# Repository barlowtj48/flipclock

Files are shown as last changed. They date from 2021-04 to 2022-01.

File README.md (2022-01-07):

# Smart Flip Clock
3D printed smart clock that puts a new twist on old technology.

Smart Flip Clock

# Making The Smart Flip Clock
The first thing that must be done for this project is to obtain all the materials that will be used. The list of things needed in this project are:
- Raspberry Pi Zero W (or any raspberry pi)
- Adequate Power Supply for Pi
- Stepper Motors (linked below)
- 3D printer and filament
- Wire
- Ability to Solder
- Glue
- Mechanical key switch from a keyboard

This design uses 4 stepper motors that can be powered using a Raspberry Pi. An external power supply is better, however they will work fine without one. The motors that I used in this project are the 28byj-48 steppers. They can be powered using 5v.

They can be found on Amazon at this link. https://www.amazon.com/gp/product/B015RQ97W8/ref=ppx_yo_dt_b_search_asin_title?ie=UTF8&psc=1

The entire construction of this clock is 3D printed, including the numbers and symbols on the flaps. Drawing on the flaps, or using stickers would be much easier however.

After printing the parts that are found on this GitHub, they can be assembled to fit together. The only thing that needs adjustment is the very small piece of plastic that is used to hold each flap in position. By design, this piece is meant to be bent after the fact to an amount that holds them sufficiently. Here's the correct number of parts that you'll need for the full assembly. If they are not listed, you only need 1 of them. 

- 56 Flaps
- 4 Drive Plates
- 4 Top Rings (to hold each of the 14 flaps onto their central shaft)
- 4 Flap Gear shafts
- 4 Drive Gears
- 4 Idle Gears
- 4 Idle Gear Holders (look like washers)
- 8 Bolts (printed)
- 4 Frame braces (optional if you're using the flap restrictor)

For the larger parts, I've included 2 options for those who are trying to print this with a smaller print bed. Option 1 is to come up with something on your own, and use the STEP files that are in the STEP files folder. Option 2 is to use the parts labeled `clock_part_split0.stl`. These are cut up to fit onto beds that are 150mm, to make sure that everyone can print them. 

In the code (and before putting labels on), make sure to test the code after plugging in the motors. If they do not rotate smoothly, you have likely ordered the pins incorrectly. Add a `time.sleep(1)` command where the clock increments each step of the motor. This will indicate what stage in the step that the motor is in. The LEDs on the controller board should light up to reflect its current stage. They should follow this order. 1 for on, 0 for off. 

0:   `1 0 0 0`\
1:   `1 1 0 0`\
2:   `0 1 0 0`\
3:   `0 1 1 0`\
4:   `0 0 1 0`\
5:   `0 0 1 1`\
6:   `0 0 0 1`\
7:   `1 0 0 1`

If this is not true, ensure that the correct pins are in order in the code. 

After this holds true for all 4 steppers, then you are good to attack the motors to the clock frame with the plastic bolts and glue.

A button is also included, I used an old mechanical key switch that was laying around. This is used to operate the clock.
It is connected as a closed loop to the raspberry pi. The switch is attached to GPIO pin 24, and to ground. The orientation should not matter. It is used as a trigger in the code to display the weather, and pause/stop the clock when held for longer durations. 

Make sure that the following packages are installed on the system, so that the code is able to locate itself and give accurate weather information. This is done with the following commands. 
`sudo pip3 install geocoder`
For the Pi Zero, the following command must be run to obtain the GPIO package.
`sudo apt-get update
sudo apt-get install rpi.gpio`

Before the code will run, you must first obtain an API key from https://openweathermap.org/api (free). This is needed to fetch the weather for your area. Take the key that is generated from your account, and put it in the place of `api_key = "YOUR_API_KEY_HERE"` in the code (line 122). This will give the python code access to the weather data. 

Upload the code to the Pi, and run the command `sudo nohup flipclock.py`. This will get the code to run in the background on the pi. 

There are 4 "modes" of the clock. Right as the script starts, it's in its default mode of showing the time. When the button is pressed, it will show the weather for an amount of time you can set for yourself, default is 10 seconds. To pause the clock, hold the button for more than 2 seconds but less than 10. To unpause, just press the button again. To set the flaps back to their 'resting' state, 0000, hold the button for 10 seconds. This will also end the python script.

## Assembly
If you've printed the number of pieces directed above, then assembly should be a relatively-simple puzzle to assemble. To assist, here are photos of the rear of my clock that should help to clear up any confusion if you have any.

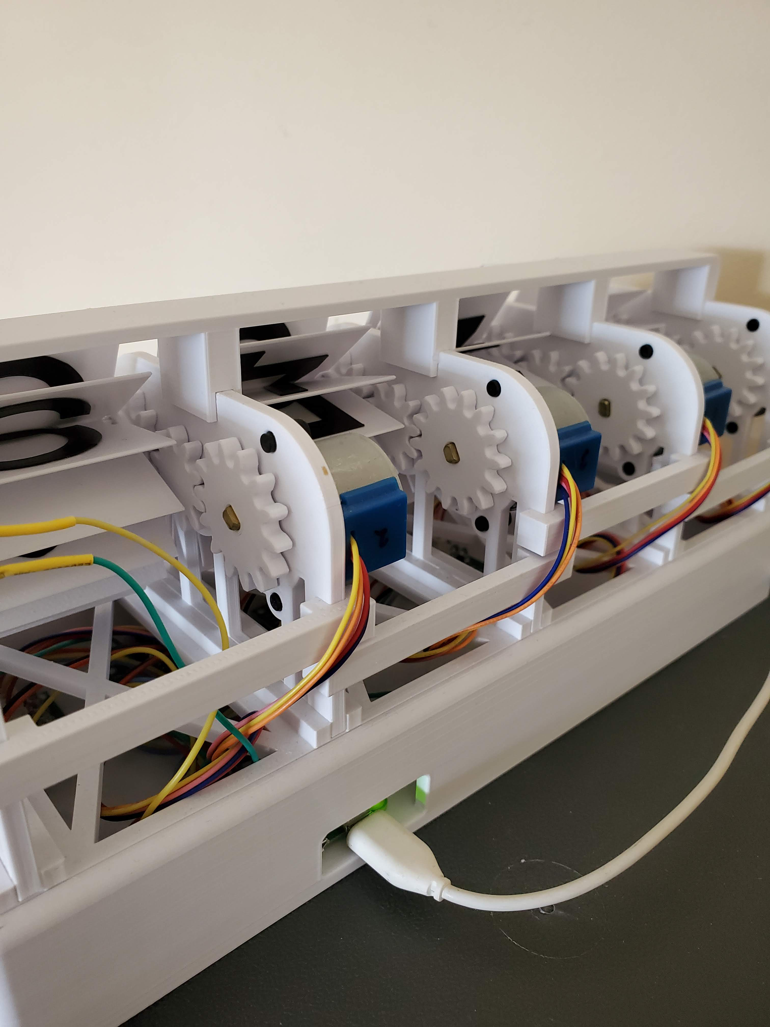
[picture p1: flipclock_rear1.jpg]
Flipclock Rear Photo 1


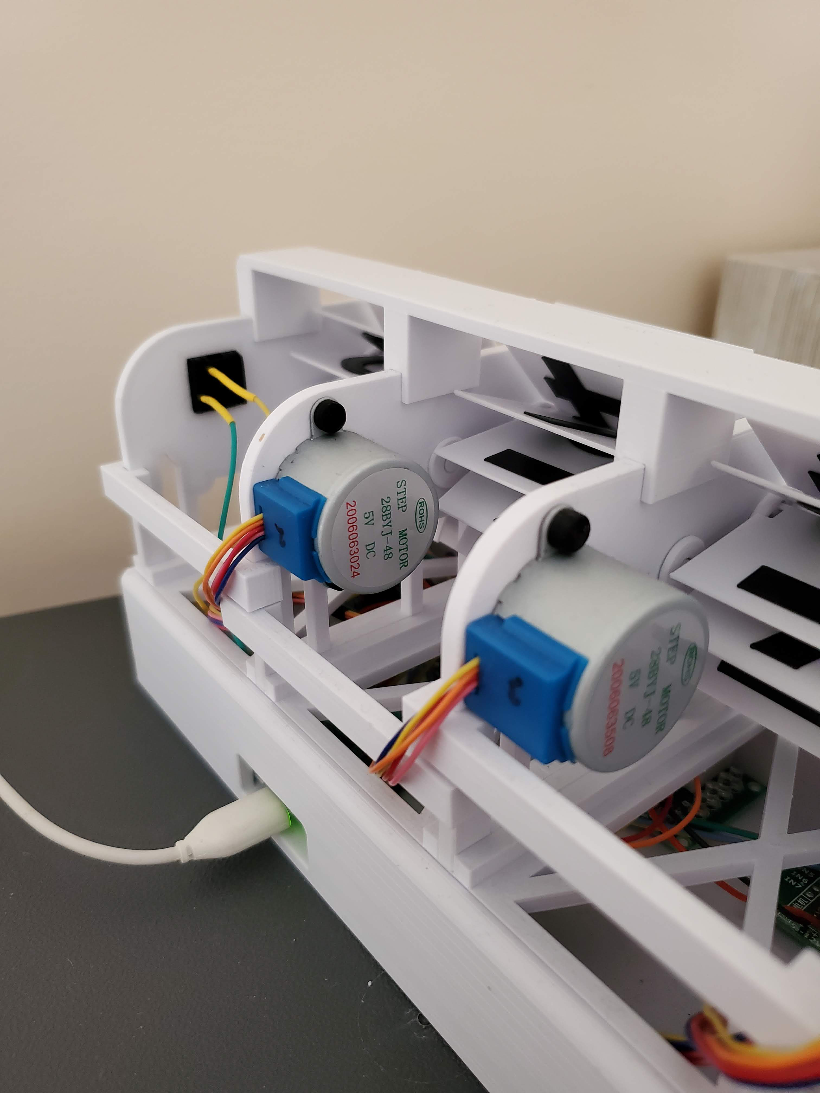
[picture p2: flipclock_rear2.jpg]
Flipclock Rear Photo 2


To read more about my time designing this and printing it, visit [my website](https://thomasjbarlow.com/flip_clock).
If you have any questions about this, feel free to email me! You can find my email easily from the above link.

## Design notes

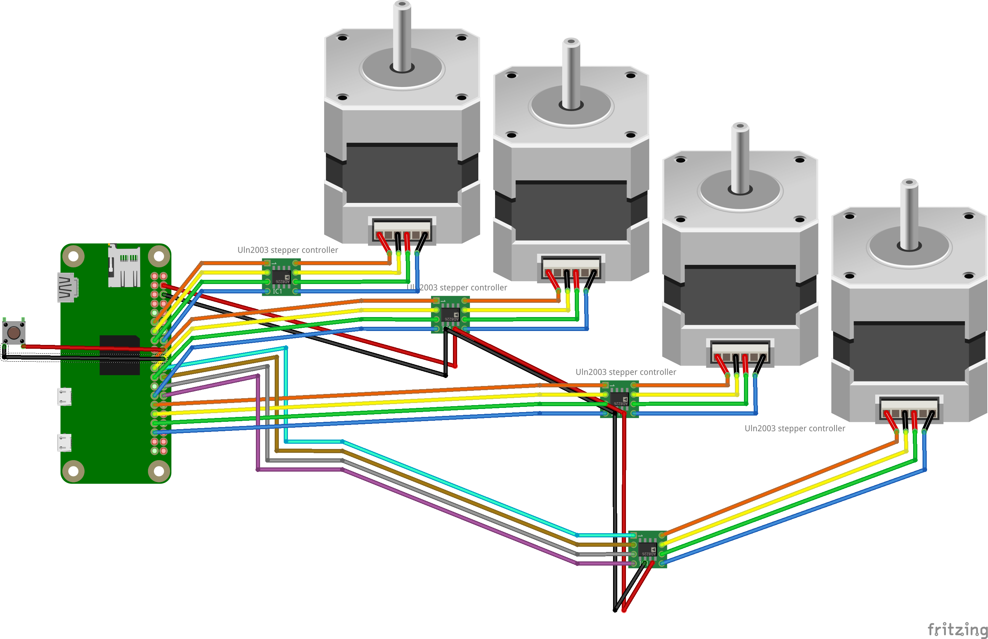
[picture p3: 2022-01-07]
flipclock_schematic.png

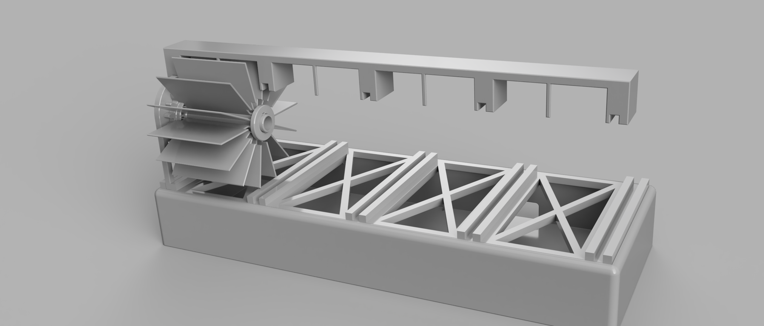
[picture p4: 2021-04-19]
flip_clock_stls/Render/FlipClock_Frame_2021-Jan-27_08-05-05PM-000_CustomizedView24092891461.png

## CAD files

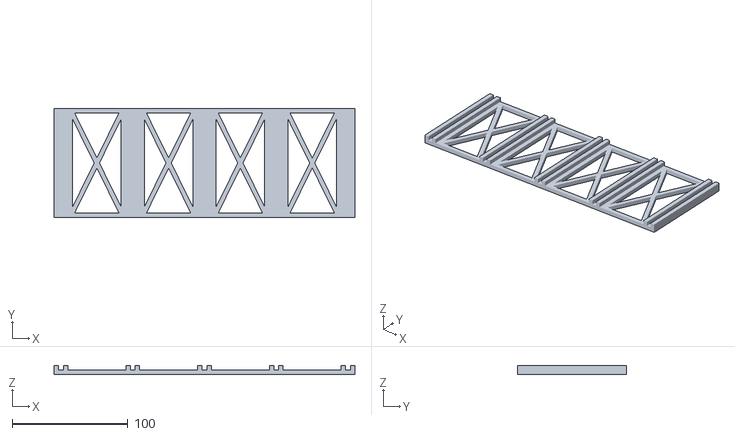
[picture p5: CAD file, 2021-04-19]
flip_clock_stls/FullFrameBrace.stl
260.0 x 94.0 x 8.00

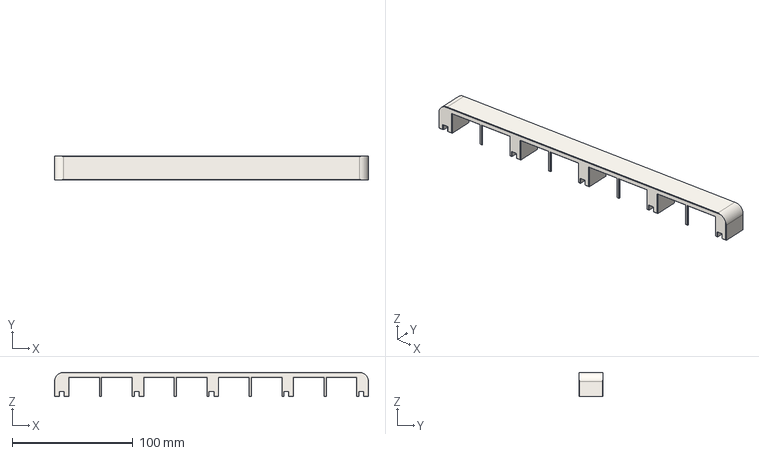
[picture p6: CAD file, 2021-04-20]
flip_clock_step/FlipClock_Flip_Restrictor.step
260.0 x 20.0 x 20.0 mm

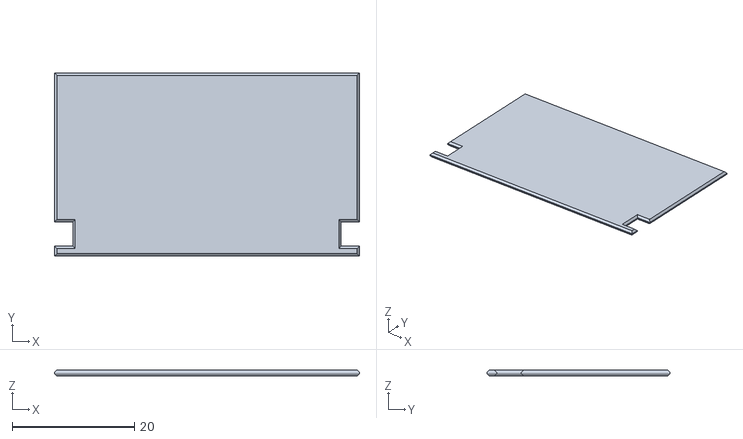
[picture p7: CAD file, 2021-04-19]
flip_clock_stls/Flap.stl
50.0 x 30.0 x 1.00

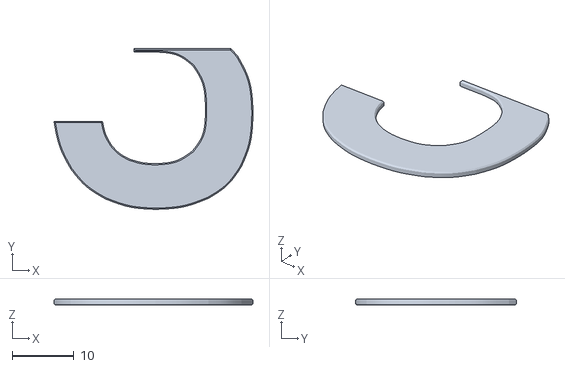
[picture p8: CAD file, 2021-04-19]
flip_clock_stls/Numbers/three2.stl
32.3 x 26.1 x 1.00

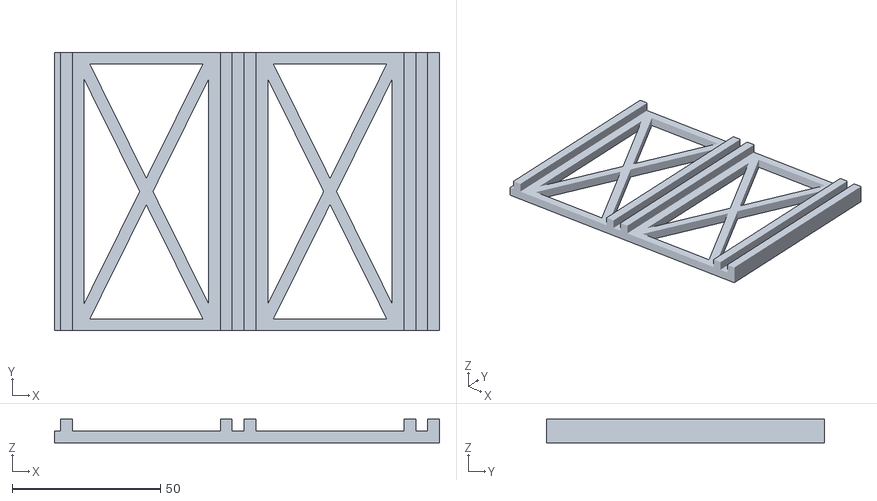
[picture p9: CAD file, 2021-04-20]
flip_clock_stls/split_parts/FrameBrace_split0.stl
130.0 x 94.0 x 8.00

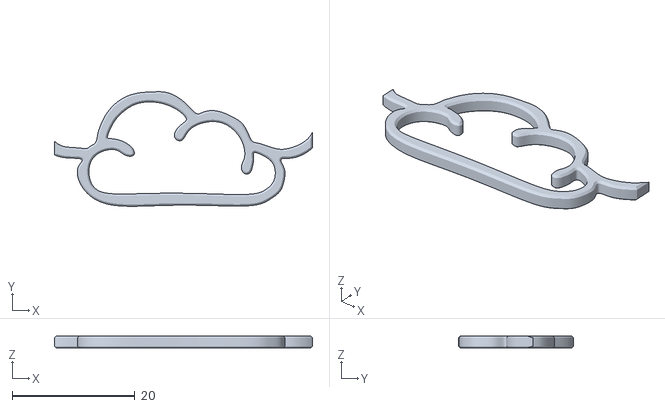
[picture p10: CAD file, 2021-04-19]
flip_clock_stls/Symbols/13_4.stl
42.0 x 18.7 x 2.00

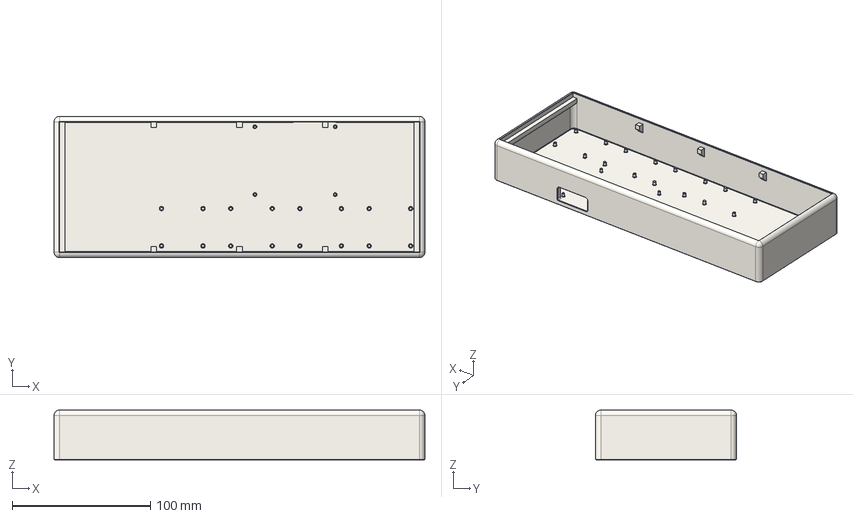
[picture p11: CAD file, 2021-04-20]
flip_clock_step/FlipClock_Base.step
268.0 x 102.0 x 36.0 mm

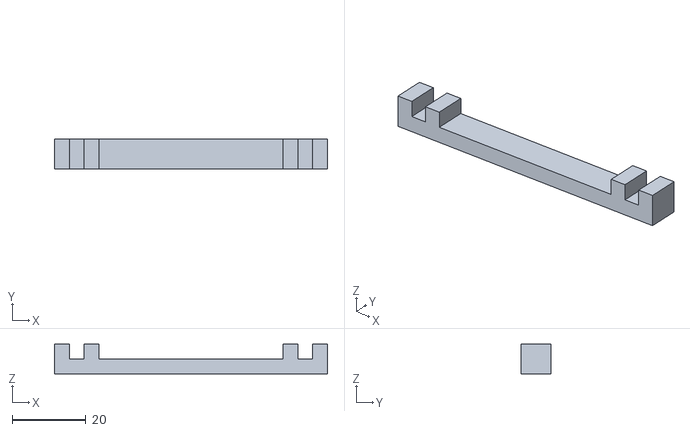
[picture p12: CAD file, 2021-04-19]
flip_clock_stls/FrameBrace.stl
74.0 x 8.00 x 8.00

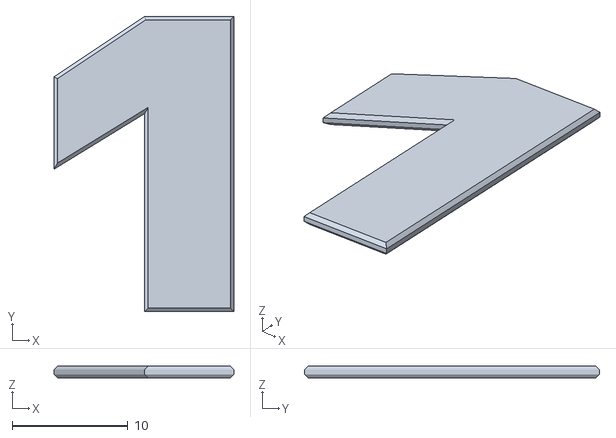
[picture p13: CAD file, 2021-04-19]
flip_clock_stls/Numbers/one1.stl
15.5 x 25.5 x 1.00

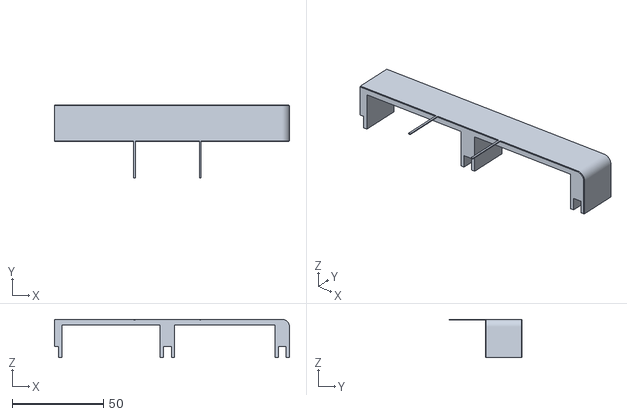
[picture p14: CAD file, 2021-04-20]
flip_clock_stls/split_parts/FlipRestrictor_split0.stl
129.0 x 40.0 x 21.0

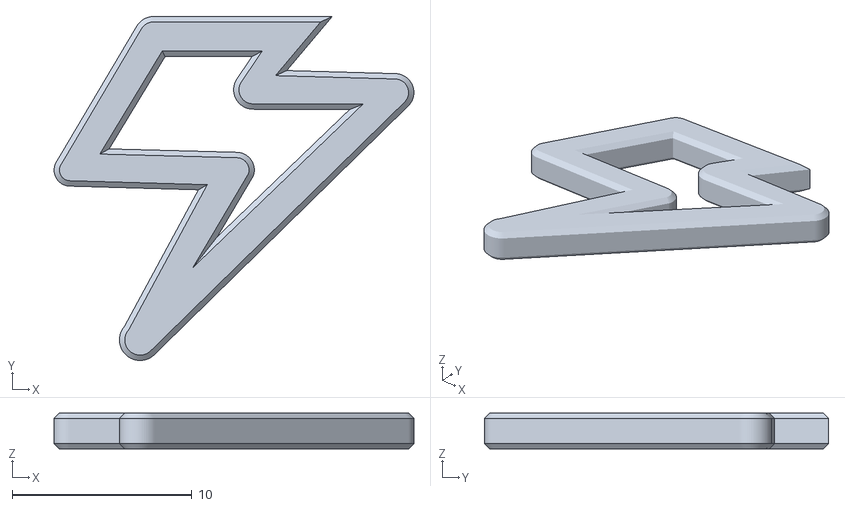
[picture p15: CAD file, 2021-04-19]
flip_clock_stls/Symbols/11_5.stl
20.0 x 19.1 x 2.00

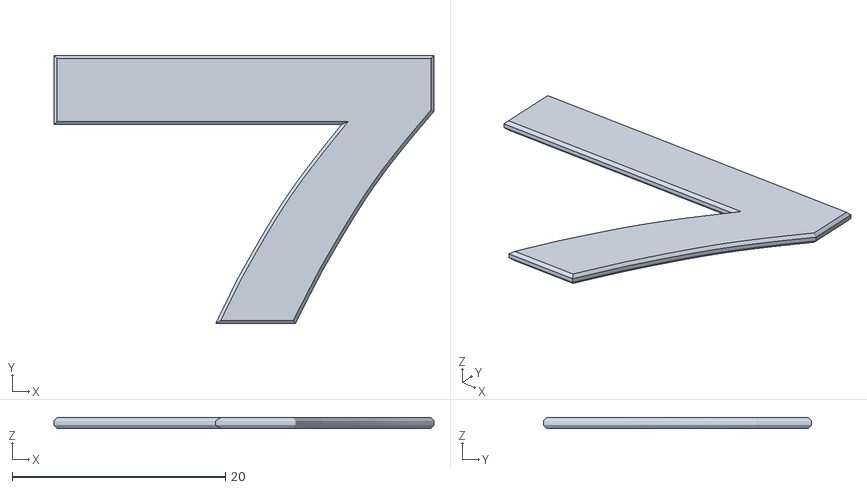
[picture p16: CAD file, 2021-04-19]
flip_clock_stls/Numbers/seven1.stl
35.6 x 25.1 x 1.00

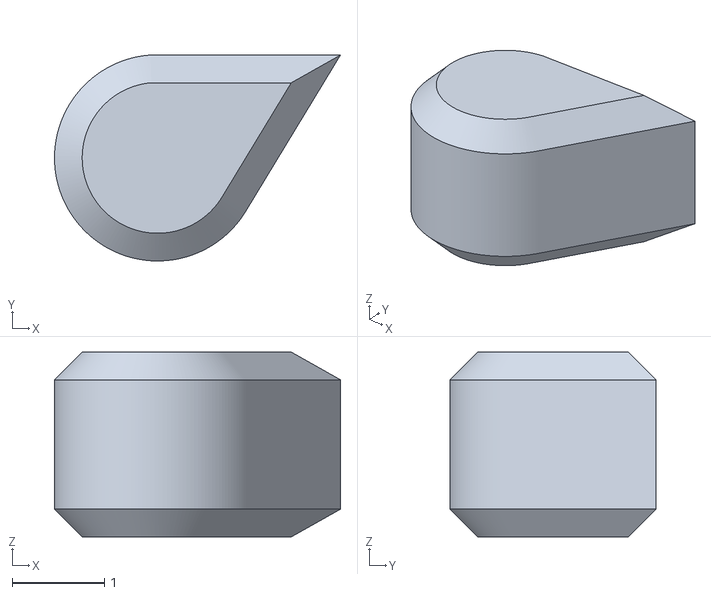
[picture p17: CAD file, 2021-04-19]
flip_clock_stls/Symbols/9_5.stl
3.09 x 2.23 x 2.00

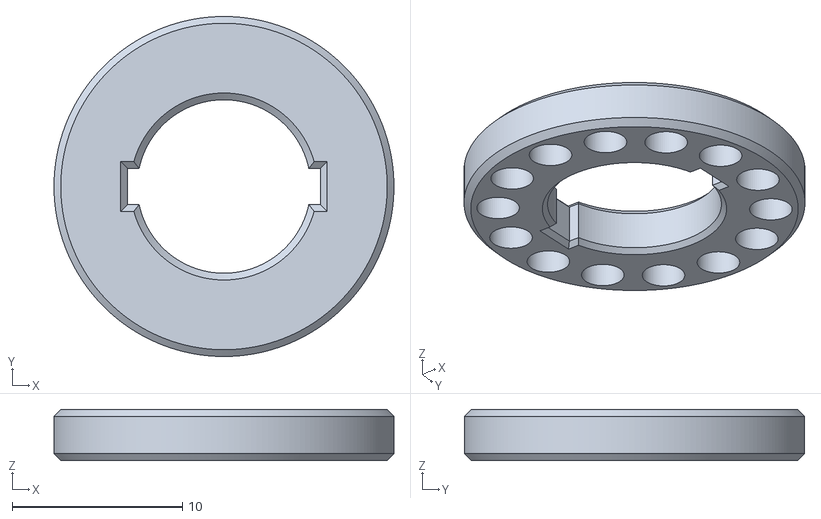
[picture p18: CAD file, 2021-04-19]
flip_clock_stls/TopRing.stl
20.0 x 20.0 x 3.00

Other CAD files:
flip_clock_step/FlipClock_FrameBase.step
flip_clock_stls/split_parts/FlipRestrictor_split1.stl
flip_clock_stls/IdleGearHolder.stl
flip_clock_stls/Numbers/five2.stl
flip_clock_stls/Bolt.stl
flip_clock_stls/Button.stl
flip_clock_stls/ButtonPlate.stl
flip_clock_stls/DriveGear.stl
flip_clock_stls/DrivePlate.stl
flip_clock_stls/FlapGear.stl
flip_clock_stls/FlipRestrictor.stl
flip_clock_stls/FrameBody.stl
flip_clock_stls/IdleGear.stl
flip_clock_stls/Numbers/eight1.stl
flip_clock_stls/Numbers/eight2.stl
flip_clock_stls/Numbers/five1.stl
flip_clock_stls/Numbers/four1.stl
flip_clock_stls/Numbers/four2.stl
flip_clock_stls/Numbers/four3.stl
flip_clock_stls/Numbers/nine1.stl
flip_clock_stls/Numbers/nine2.stl
flip_clock_stls/Numbers/nine3.stl
flip_clock_stls/Numbers/one2.stl
flip_clock_stls/Numbers/seven2.stl
flip_clock_stls/Numbers/six1.stl
flip_clock_stls/Numbers/six2.stl
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

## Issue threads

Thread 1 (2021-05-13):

How to synchronize flaps position with time and weather

SemperVis, 2021-05-13:
Hi! First of all, great project! I think it looks really cool and it's a fun thing to print or to gift.

That said, I'm having a bit of an hard time trying to synchronize the position of the flaps with the time and the weather symbols.
I tried assembling everything together, then holding the button for 10s to bring the flaps to their resting state, marking this position with 0 and starting the script again but the time shown is not what I expected.
Is the resting state meant to be all blank on flaps or the number zero?
Also, if the Pi loses power (and so the motors) when I turn on the clock again, it obviously resets and shows the incorrect numbers, is there a solution for this?

Thank you so much for the project!

barlowtj48, 2021-05-13:
Thanks for your interest in the clock!

The script starts outputting the time immediately after it starts. This is assuming that the flaps are all at 0000. The order of the flaps are as follows:
0, 1, 2, 3, 4, 5, 6, 7, 8, 9, A, B, C, D, where A is blank, and B, C, D, are weather icons.

When the clock is paused, holding the button for a short time (less than 10s), it goes to AAAA (all blank), however holding for 10s will bring the clock back to it's fully power-off state of 0000. If you know how to change the script, then this can also be done one flap at a time, for example `Output("4000")` if you need to rotate the first flap 4 times. After this function be sure to add `quit()` so that it does not continue to output the time.

Hope this helps.

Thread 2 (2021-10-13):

Clock reset.

nicknamemok, 2021-10-13:
Hey your project looks awesome! I'm just peeking at your code and wanted to ask something.
If you unplug the clock without putting it at 'rest' position (i.e. holding the button for 10 seconds), does the clock function properly after re-plugging it in? Thanks!

nicknamemok, 2021-10-15:
Thanks for the response!
Hall-effect or an encoder would both do the trick, but then that would kind of take the budget of this thing too high.
I am thinking maybe microswitches could do the trick? But I'm not sure, we will see!

Closed 2021-10-15.

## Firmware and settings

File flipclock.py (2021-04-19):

# Developed by Thomas Barlow
# Free for Private Use
# More information at https://thomasjbarlow.com/flip_clock


import RPi.GPIO as GPIO
import time
from enum import Enum
import datetime
import geocoder
import json
import requests

Flip_To = Enum("Flip_To", ["0", "1", "2", "3", "4", "5", "6", "7", "8", "9", "A", "B", "C", "D"], start=0)
weather_associations = {1 : "AD",
                        2 : "AC", 
                        3 : "AB", 
                        4 : "AB", 
                        9 : "BB", 
                        10: "BC", 
                        11: "CB", 
                        13: "DB", 
                        50: "AB"}

class ServoController:
    def __init__(self, m_servos):
        self.servos = m_servos
        self.sub_steps = [[0, 0, 0, 1],
                            [0, 0, 1, 1],
                            [0, 0, 1, 0],
                            [0, 1, 1, 0],
                            [0, 1, 0, 0],
                            [1, 1, 0, 0],
                            [1, 0, 0, 0],
                            [1, 0, 0, 1]]
        self.step_order = [36, 37, 36, 37, 36, 37, 36, 37, 36, 37, 36, 37, 37, 37]

    def servos_done(self):
        done = 0
        for i in range(4):
            if(self.servos[i].done):
                done += 1
        if done == 4:
            for i in range(4):
                self.servos[i].done = False
            return True
        else:
            return False

    def sum_step_order(self, index, distance):
        added = 0
        for i in range(distance):
            added += self.step_order[index]
            index += 1
            if(index == 14):
                index = 0
        return added

    def get_total_steps(self, output_str):
        output = [str(d) for d in str(output_str)]
        steps = []
        for i, val in zip(range(4), output):
            index_offset = self.servos[i].get_flap_offset(Flip_To[val].value)
            steps.append(self.sum_step_order(self.servos[i].current_flap, index_offset))
        return steps

    def Output(self, output_str):
        total_steps = self.get_total_steps(output_str)
        while(not self.servos_done()):
            for substep in self.sub_steps:
                for i in range(4):
                    if(not self.servos[i].current_step == total_steps[i]):
                        self.servos[i].substep(substep)
                    else:
                        self.servos[i].done = True
                        self.servos[i].stop()

                time.sleep(.001)

class Servo:
    def __init__(self, m_pins):
        self.pins = m_pins
        self.current_flap = 0
        self.current_step = 0
        self.current_substep = 0
        self.done = False

    def stop(self):
        for i in range(4):
            GPIO.output(self.pins[i], 0)
    
    def substep_increment(self):
        if(self.current_substep == 7):
            self.current_substep = 0
            self.current_step += 1
            if(self.current_step == 512):
                self.current_step = 0
        else:
            self.current_substep += 1

    def substep(self, step):
        for pin, bit in zip(self.pins, step):
            GPIO.output(pin, bit)
        self.substep_increment()
    
    def get_flap_offset(self, index):
        offset = 0
        if(index < self.current_flap):
            offset = (14-self.current_flap) + index
        else:
            offset = index - self.current_flap
        return offset
        
def format_time():
    now = datetime.datetime.now()
    output = str(now.strftime("%I%M"))
    if(output[0] == "0"):
        output = "A" + output[1:]
    return output

def format_weather():
    api_key = "YOUR_API_KEY_HERE"
    location = geocoder.ip('me')
    url = "https://api.openweathermap.org/data/2.5/onecall?lat={lat}&lon={lon}&exclude={part}&appid={api}".format(lat=location.latlng[0], lon=location.latlng[1], part="hourly,minutely,alerts,daily", api=api_key)

    response = requests.get(url)
    data = response.json()

    temperature = float(data['current']['temp'])
    icon = data['current']['weather'][0]['icon'][:-1]

    temperature = round((temperature - 273.15) * 9/5 + 32)
    temperature = "{:02d}".format(temperature)
    icon = weather_associations[int(icon)]

    output = str("{}{}".format(temperature, icon))
    return output

# Flap 0 pins on raspberry pi: 17, 27, 22, 23
# Flap 1 pins on raspberry pi: 10, 9,  11, 0
# Flap 2 pins on raspberry pi: 5,  6,  13, 19
# Flap 3 pins on raspberry pi: 25, 8,  7,  1
# as you can see in the line below, any GPIO pin will work, as long as they are associated correctly here in the code. 
servos = [Servo([17, 27, 22, 23]), Servo([10,9,11,0]), Servo([5,6,13,19]), Servo([25,8,7,1])]
sc = ServoController(servos)

GPIO.setmode(GPIO.BCM)
GPIO.setup(24, GPIO.IN, pull_up_down=GPIO.PUD_UP)
GPIO.setwarnings(False)
for servo in servos:
    for i in servo.pins:
        GPIO.setup(i, GPIO.OUT)

while(True):
    duration = 0
    while(GPIO.input(24) == False):
        duration += .01
        time.sleep(.01)
    if(duration > .1 and duration < 1):
        sc.Output(format_weather())
        time.sleep(10)
    elif(duration > 2 and duration < 10):
        time.sleep(1)
        while(GPIO.input(24) == True):
            sc.Output("AAAA")
        time.sleep(2)
    elif(duration > 10):
        sc.Output("0000")
        quit()
    else:
        sc.Output(format_time())

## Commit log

2021-04-19 add stl files
    [01_1.stl, 01_2.stl, 02_1.stl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]
2021-04-19 added schematic explanation
2021-04-19 add schematic
2021-04-20 add big parts so people can split them as they like
    [FlipClock_Base.step, FlipClock_Flip_Restrictor.step, FlipClock_FrameBase.step]
2021-04-20 add split parts for smaller printers
    [FlipRestrictor_split0.stl, FlipRestrictor_split1.stl, FrameBody_split0.stl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]
2021-08-17 Update README.md
    added better description for control button
2022-01-07 Add button to schematic diagram
2022-01-07 add photos of rear for assembly
